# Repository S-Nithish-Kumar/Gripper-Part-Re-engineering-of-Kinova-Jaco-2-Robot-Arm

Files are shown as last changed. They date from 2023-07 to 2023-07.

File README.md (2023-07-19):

<h2 align="center">Demonstration Video</h2>
<p align="center">
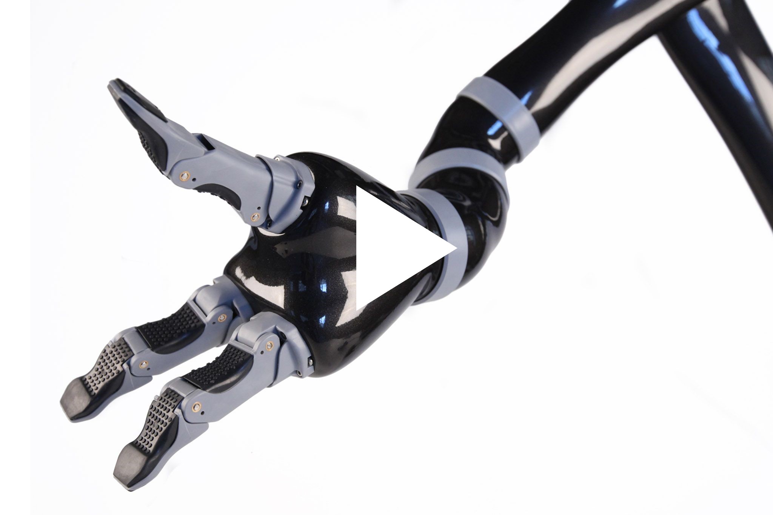
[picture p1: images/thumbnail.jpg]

</p>

## Contents:
<ol>
   <li><a href="https://s-nithish-kumar.github.io/Gripper-Part-Re-engineering-of-Kinova-Jaco-2-Robot-Arm/#1-problem-statement">Problem Statement</a></li>
   <li><a href="https://s-nithish-kumar.github.io/Gripper-Part-Re-engineering-of-Kinova-Jaco-2-Robot-Arm/#2-objectives">Objectives</a></li>
   <li><a href="https://s-nithish-kumar.github.io/Gripper-Part-Re-engineering-of-Kinova-Jaco-2-Robot-Arm/#3-design-process">Design Process</a></li>
     <li><a href="https://s-nithish-kumar.github.io/Gripper-Part-Re-engineering-of-Kinova-Jaco-2-Robot-Arm/#4-material-selection">Material Selection</a></li>
     <li><a href="https://s-nithish-kumar.github.io/Gripper-Part-Re-engineering-of-Kinova-Jaco-2-Robot-Arm/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">Impact of Solving the Problem</a></li>
   <li><a href="https://s-nithish-kumar.github.io/Gripper-Part-Re-engineering-of-Kinova-Jaco-2-Robot-Arm/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">Results and Conclusion</a></li>
</ol>

### 1. Problem Statement:
- Due to wear and tear and ageing factors, the internal part of the Kinova Jaco 2 Robot Arm is damaged.
* The internal part has varying levels of flexibility in different regions and should be considered while designing and manufacturing. Fig shows the flexibility variations in different parts of the component.
<p align="center">
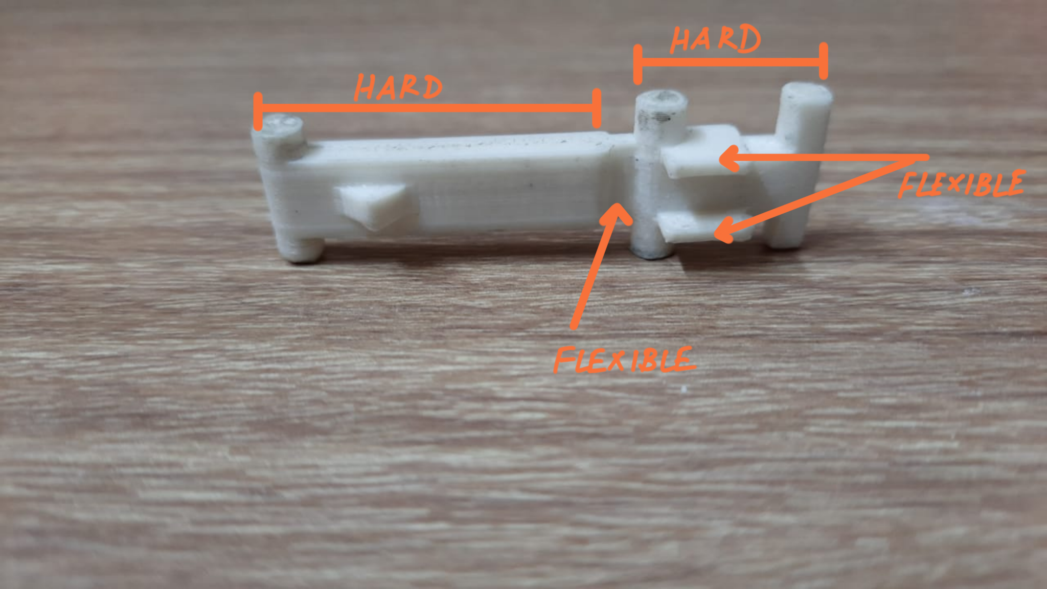
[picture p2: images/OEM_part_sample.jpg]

</p>

### 2. Objectives:
- To redesign the gripper part by measuring the part dimensions manually using a Vernier Caliper.
* Divide the part into two and design a hinge which will act as a replacement for the flexible portion of the component.
+ Select proper materials for 3D printing the part.

### 3. Design Process:
- Thermoplastic Polyurethane (TPU) with shore A hardness of 87 is chosen as the print material and printed with the 3D design below. But TPU being soft was flexible even in the longer part of the component which makes it incompatible for use with the gripper.
<p align="center">
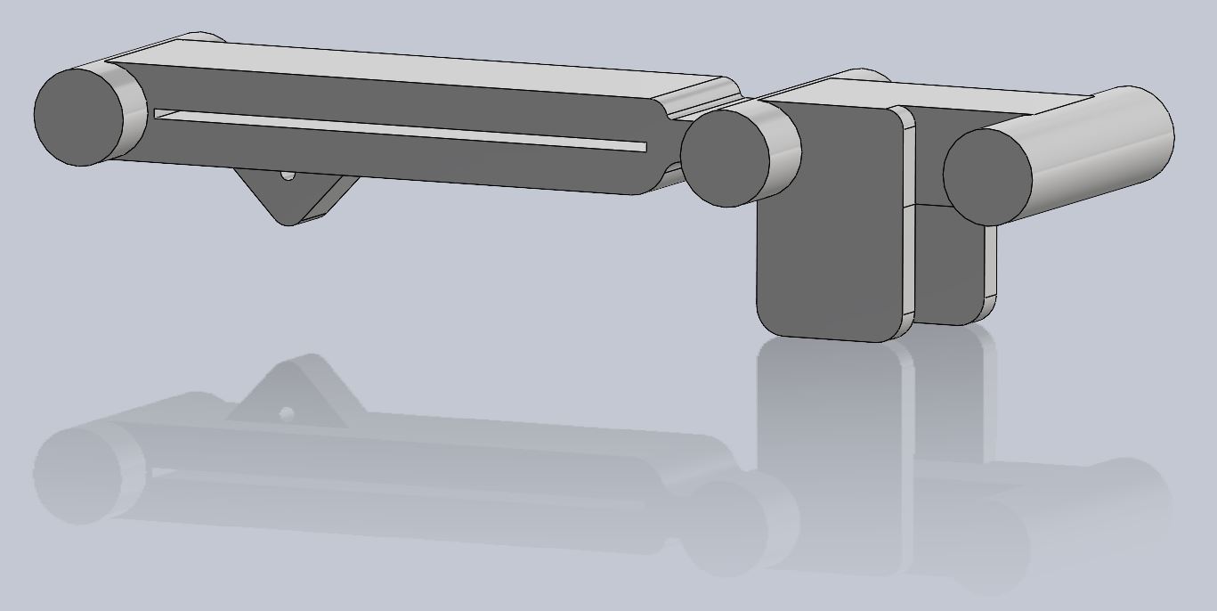
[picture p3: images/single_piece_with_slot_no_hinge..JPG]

</p>
* To increase the flexibility of the longer part, a slot was provided in it which can be filled with a thin metal plate to increase the rigidity. But due to the printer’s limited accuracy and the smaller size of the component the finishing of the part was not good and cannot be used for assembly.
<p align="center">
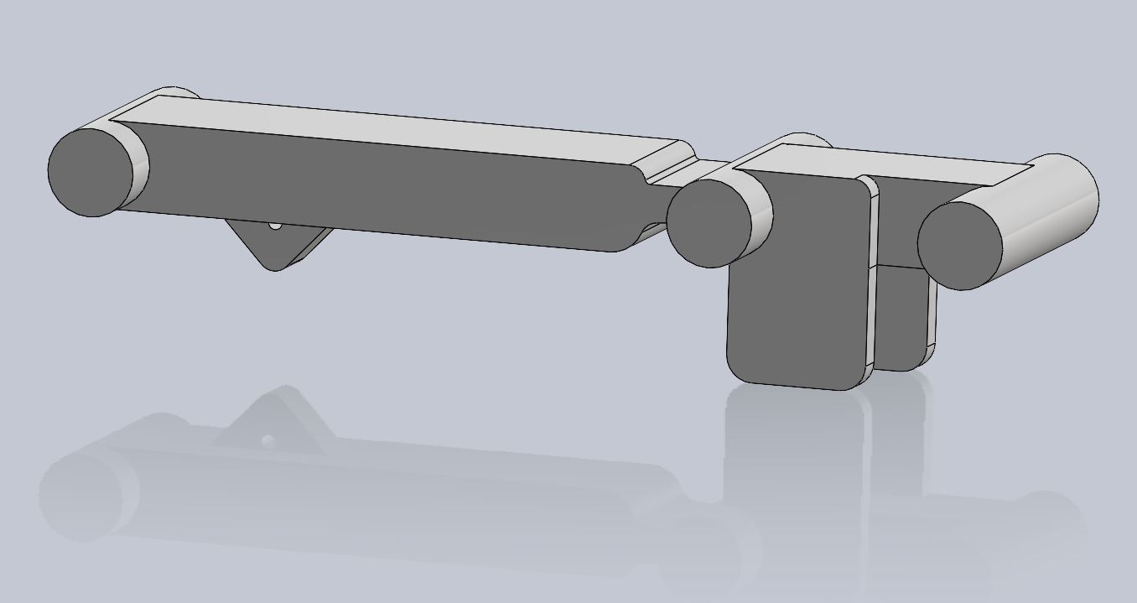
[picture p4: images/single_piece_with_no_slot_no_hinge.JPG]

</p>
+ To overcome the problem with the above designs, the component has to be divided into two parts with different materials for each part. The material selection section shows the third design with two different materials each for smaller and longer parts.

### 4. Material Selection:
The printed component has two parts in total:
* The smaller part is printed with Thermoplastic polyurethane (TPU) with shore A hardness of 87
- The longer part is printed with Polylactic acid (PLA)
+ Figure below shows the 3D design of the component. The two different parts are combined with a stainless steel rod.
<p align="center">
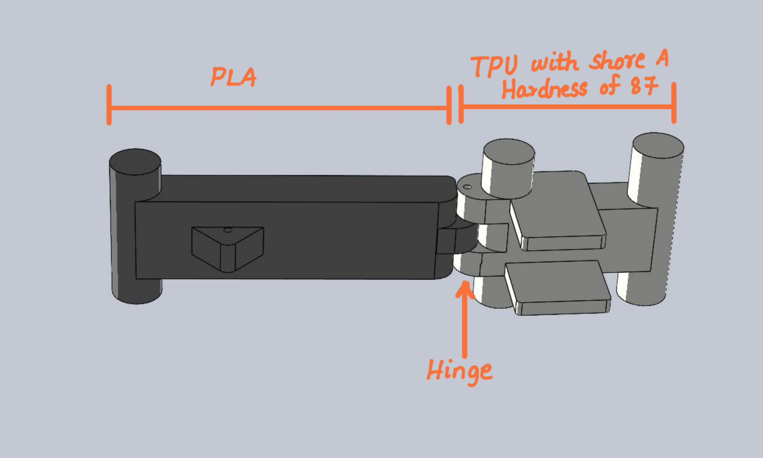
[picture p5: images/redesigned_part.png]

</p>

### 5. Impact of Solving the Problem:
- The replaced part will be a temporary solution for the gripper to perform most of the tasks as how the gripper works with the OEM’s part.
+  The cost of the replaced part using 3D printing is 50 times less than the OEM’s product. This is because the entire finger has to be replaced and the damaged part alone can’t be replaced by the OEM.

### 6. Results and Conclusion:
- The gripper is found to perform well for grasping less weighed objects. Grasping heavy objects will damage the part as more tension acts on the gripper.
+ The gripper performed well for 2 months after which the part started to damage.
* The replaced part acted as temporary solution and supported to perform most of the gripper tasks.

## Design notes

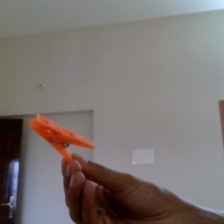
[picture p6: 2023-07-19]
images/sample_orange_class.jpg

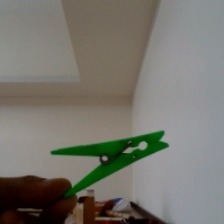
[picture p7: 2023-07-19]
images/sample_green_class.jpg

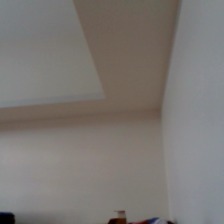
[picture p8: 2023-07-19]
images/sample_background_class.jpg

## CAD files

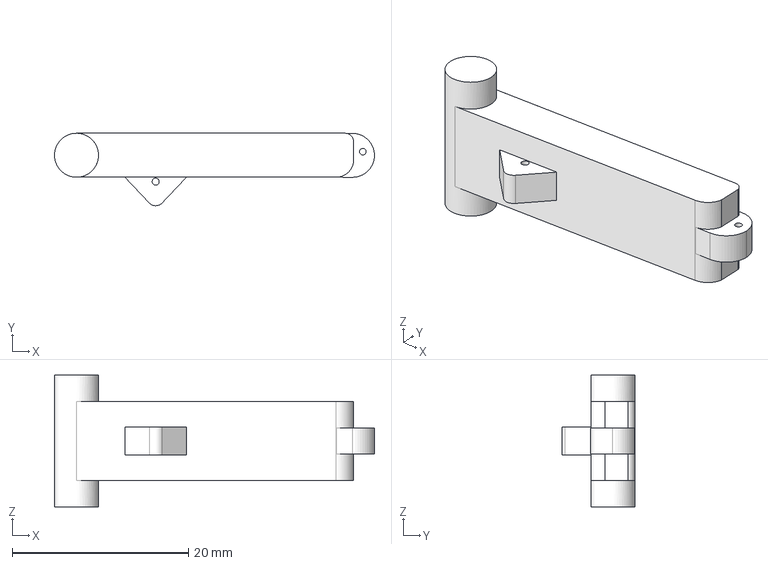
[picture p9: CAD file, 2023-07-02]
3D_models/kinova gripper longer part.step
36.4 x 8.24 x 14.9 mm

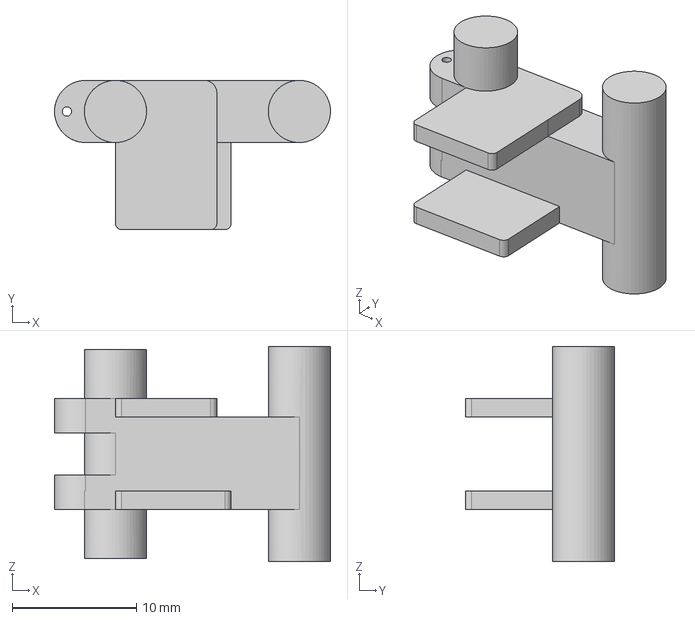
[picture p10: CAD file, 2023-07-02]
3D_models/kinova gripper small part.step
22.2 x 12.0 x 17.3 mm

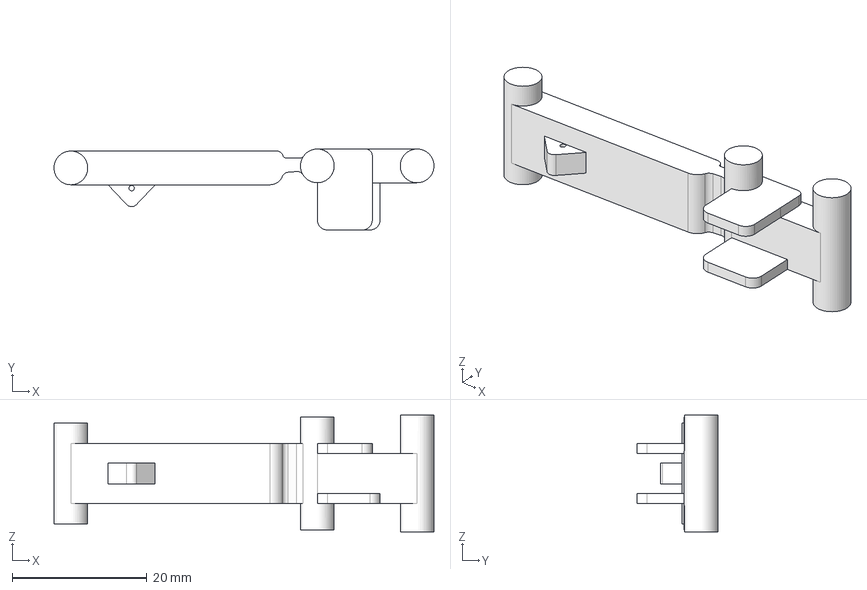
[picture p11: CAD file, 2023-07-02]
3D_models/kinova gripper part _ final (without hinge).step
56.3 x 12.0 x 17.3 mm

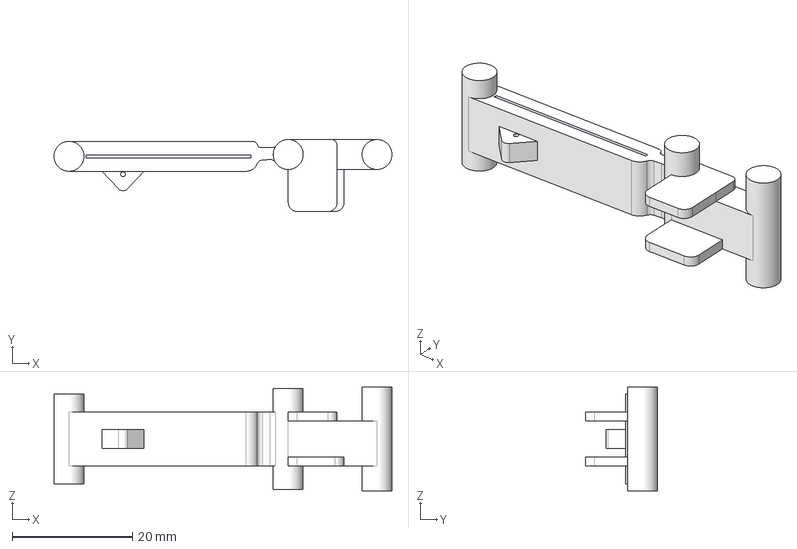
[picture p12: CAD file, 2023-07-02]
3D_models/kinova gripper part _ final_slot (without hinge).step
56.3 x 12.0 x 17.3 mm

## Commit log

2023-07-02 Added 3D models and images
    [kinova gripper longer part.step, kinova gripper part _ final (without hinge).step, kinova gripper part _ final_slot (without hinge).step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]
2023-07-19 add color samples
